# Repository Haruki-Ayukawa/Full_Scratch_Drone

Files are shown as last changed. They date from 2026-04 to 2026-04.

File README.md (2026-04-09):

# Full_Scratch_Drone
## 概要
キットを購入するのではなく<br>
- KiCADで設計し表面実装したESP32搭載制御基板
- 3DCADで設計し3Dプリンタで造形したフレーム
- AmazonやRCヘリドローン専門ショップで購入したモータ・プロペラ・LiPoバッテリ

を用いてフルスクラッチのドローンを製作しました。

## 制御基板
- 構成 → MCU(マイコン)＋IMU(9軸慣性センサ)＋ESC(MOSFET×4個)＋コネクタなどを1枚の基板に搭載しました。
- 部品 → ESP32-MINI-1-N4(MCU)、ICM-20948(IMU)、AO3400A(Nch MOSFET)などなど。
- 購入 → 秋月電子通商　様やcorestaff　様で購入しました。一部のパーツはAmazonで購入しました。
- 基板 → SnapMagicなどでパーツのデータを収集し、KiCADで回路図及びPCB基板を設計後、JLCPCBに発注しました。
- 実装 → ホットプレートやペーストはんだを用いて表面実装しました。

詳細は[control-boardフォルダ](control-board)をご覧ください。

## フレーム
- 設計 → Fusionで設計しました。
- 製造 → 3Dプリンタ(RAISE3D E2　ノズル径0.4mm　フィラメントPLA黒色)で造形しました。

詳細は[frameフォルダ](frame)をご覧ください。

## モータ
- 部品 → [直径8.5mm　長さ20mm　3~5V](https://amzn.asia/d/07lUeh3T)
- 購入 → Amazonで購入しました。

## プロペラ
- 部品 → [マイクロクワッド用55mm Blade Propeller Prop 4pcs](https://wda-jp.com/shop/products/detail/863)
- 購入 → 若狭小浜ドローン協会(WDA) 様の公式オンラインショップで購入しました。

## LiPoバッテリ
- 部品 → [GNB POWER LIPO 550mAh 1s 3.8V 100C コネクタ種：A30](https://helimonster.jp/?pid=176671622)
- 購入 → ヘリモンスター　様で購入しました。

## 制御コード(フライトコントローラ：ドローン側)
- VSCodeでコーディングし、VSCodeの拡張機能であるPlatformIOでコンパイルとビルドを行いました。

詳細は[firmwareフォルダ]()をご覧ください。

## 制御コード(プロポーショナルコントロール送信機：スマホアプリ側)
- MIT App Inventorというブラウザタイプのアプリ開発ツールを用いてスマホをドローンのプロポにしました。

詳細は別のリポジトリ[Example_MITAppInventor_for_DroneController](https://github.com/Haruki-Ayukawa/Example_MITAppInventor_for_DroneController/tree/main)をご覧ください。

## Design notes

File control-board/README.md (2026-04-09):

# control-boardフォルダの中身について
## KiCadフォルダ

## manufacturingフォルダ

## docsフォルダ

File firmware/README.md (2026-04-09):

# firmwareフォルダの中身について
## drone_PID_1フォルダ
VSCode内の拡張機能「PlatformIO」を利用してコーディング・ビルド・コンパイルを行いました。<br>
1_includeフォルダ, 2_libフォルダ, 3_platformio.iniファイル, 4_srcフォルダが入っています。<br>
以下その説明

## 1_includeフォルダ
特に使っていません。

## 2_libフォルダ
特に使っていません。

## 3_platformio.iniファイル
書き込み先のボード種やシリアル通信のbps、インクルードするライブラリを指定するファイルです。

## 4_srcフォルダ
コードの中身になります。<br>
.cppファイルは実際の関数の中身が書かれています。<br>
.hファイルは関数・定数の宣言や必要な外部ライブラリのインクルードが書かれています。<br>
以下簡単な説明

#### control.cppファイルと.h ファイル
- モータをPWMで駆動させる上でのセットアップ関数と実際に駆動させる関数
- ①madgwick.cppで得たロールピッチヨー(RPY)の姿勢角　②interfaceBLE.cppで受け取った角度あるいは角速度の目標値　を元にPID制御する関数

などが書かれています。<br>
単ループ角度PID制御とカスケード制御の両方の関数があります。

#### debug.cppファイルと.h ファイル
- PCとつないだシリアルモニタでデバッグするための関数

が書かれています。

#### imu.cppファイルと.h ファイル
- 9軸IMUセンサのセットアップ関数
- センサのジャイロ値を校正する関数
- センサの9種の値を読み取る関数
- センサにローパスフィルタを掛ける関数

などが書かれています。<br>
なおDLPFの設定を有効にしたため、代わりに4つ目のローパスフィルタを掛ける関数では実際にはフィルタを掛けていません。

#### interfaceBLE.cppファイルと.h ファイル
- BLE通信する上でのセットアップ関数
- 指令がバイナリ通信で来た際に読み取る関数
- こちらからスマホ側へNOTIFY(送信)するための無線デバッグ関数

などが書かれています。<br>
情報工学や通信工学を専攻しておらず初めての経験だったため、**最も難しく、ほとんどchatGPT頼り**になってしまいました。

#### madgwick.cppファイルと.hファイル
- imu.cpp内の読み取り関数で得た9種(6種)の値を元にRPYの姿勢角を計算する関数

が書かれています。<br>
MadgwickfilterAHRS.hライブラリの関数をそのまま使っています。
- ①9軸(ジャイロ3軸＋加速度3軸＋地磁気3軸)
- ②6軸(ジャイロ3軸＋加速度3軸)

①か②か選択できますが、地磁気はモータ回転で発生する電磁場の影響などで上手く行かなかったため現在は②で計算しています。

#### main.cppファイル
- 上記の各種セットアップに関する関数を実行するvoid setup()関数
- BLE通信で指令値更新 → センサの読み取り → MWFで姿勢角取得 → PID計算してモータ出力 → 各種デバッグ送信　を回すvoid loop()関数

が書かれています。<br>
細かい動作仕様は[Example_MITAppInventor_for_DroneController](https://github.com/Haruki-Ayukawa/Example_MITAppInventor_for_DroneController/tree/main)
内のREADMEから飛べるYouTube動画も併せてご覧ください。

#### struct.hファイル
今回のドローンコードでは値の受け渡しに構造体を採用しています。<br>
関連するパラメータを一つのまとまりとして管理でき、コードの可読性および拡張性が向上します。<br>  
特にドローン制御では、位置・速度・姿勢といった多次元データを扱うため、構造体によるデータ管理が適していると考えました。 <br> 
<br>
このファイルでは、各種データ構造の定義を行っています。

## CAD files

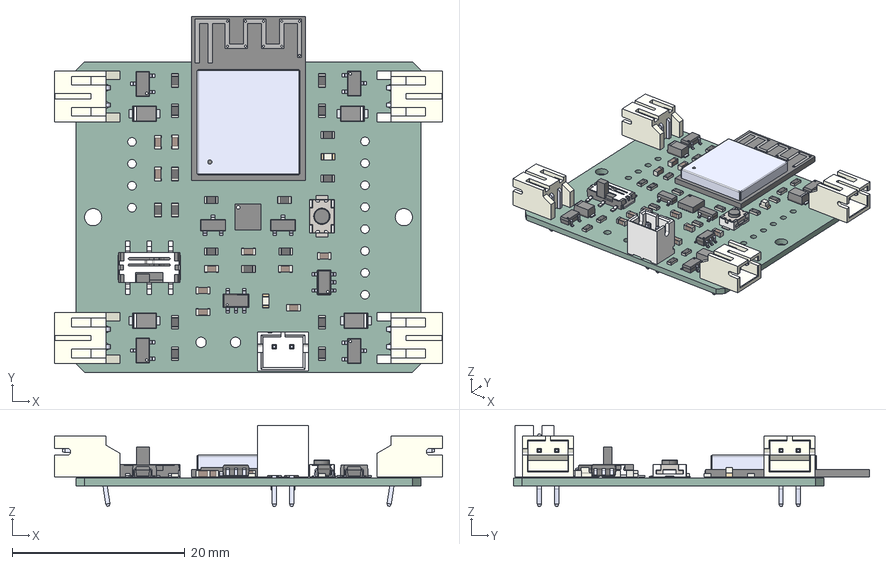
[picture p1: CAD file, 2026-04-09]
control-board/docs/drone_v0-00_pcb.step
45.0 x 41.2 x 9.40 mm
kicad_embedded_EFB9EB6B69339B4832CF7C8FAE120CEA
C_0603_1608Metric x 10
R_0603_1608Metric x 18
PinKIdent x 4
PinK x 4
PinA x 4
kicad_embedded_1087D84B1A9B50382FE17C0D6D803E1A x 4
kicad_embedded_F61AE14A9B6CD33695C6B15B4C50FB9C
LED_0603_1608Metric x 2
kicad_embedded_96822C8A4A191643E8612697CA9D3853
kicad_embedded_640A4FFACB3C051AC2F3E19E366DE6D8
kicad_embedded_2836B2736456D9190677AFF275D22C36
kicad_embedded_1FE01337C3ABB1394D092E43585B70D1 x 4
kicad_embedded_5C4911B6E682F9ABB571BB254287C6B1
kicad_embedded_445924E2E9928FB5B242DCD9D2B32355 x 2
kicad_embedded_AEB765CD93CE368EA6921F6A5A5118E1
drone_v0-01_PCB

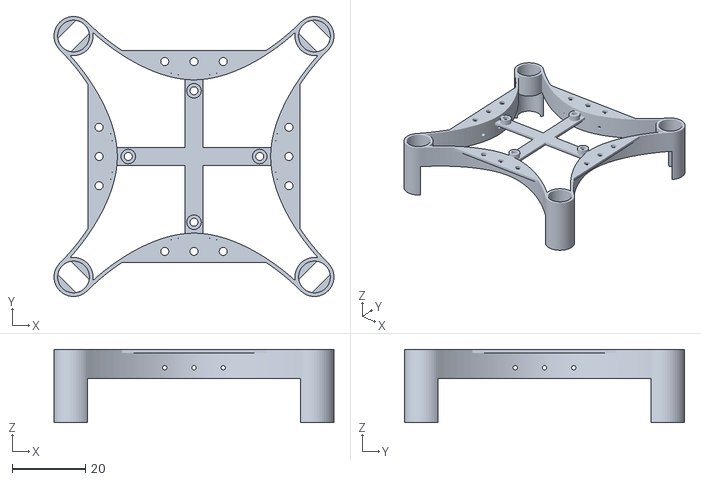
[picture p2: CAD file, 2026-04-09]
frame/drone_v0-03_frame.stl
76.7 x 76.7 x 20.0

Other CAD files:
frame/drone_v0-03_frame.f3d

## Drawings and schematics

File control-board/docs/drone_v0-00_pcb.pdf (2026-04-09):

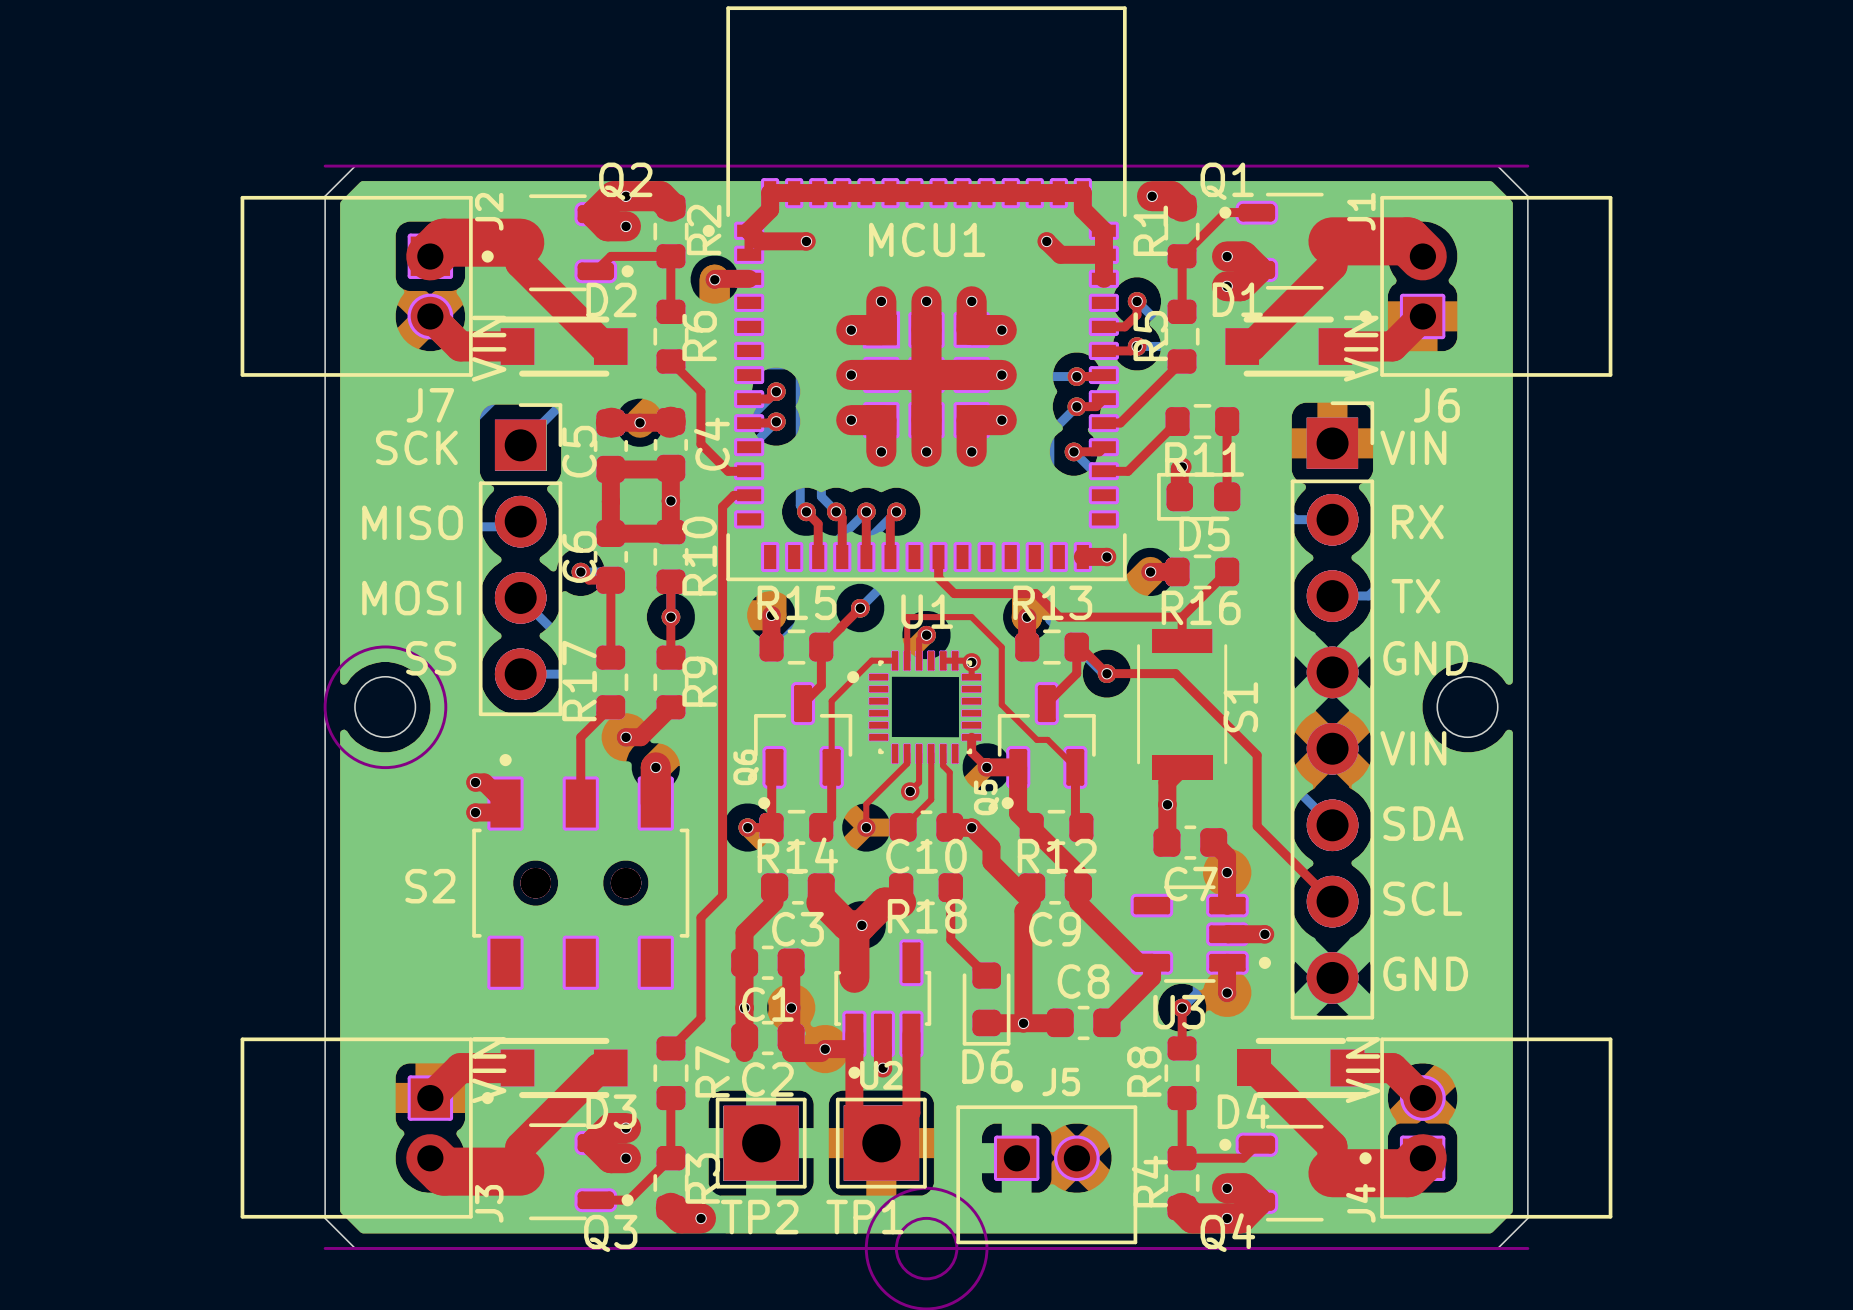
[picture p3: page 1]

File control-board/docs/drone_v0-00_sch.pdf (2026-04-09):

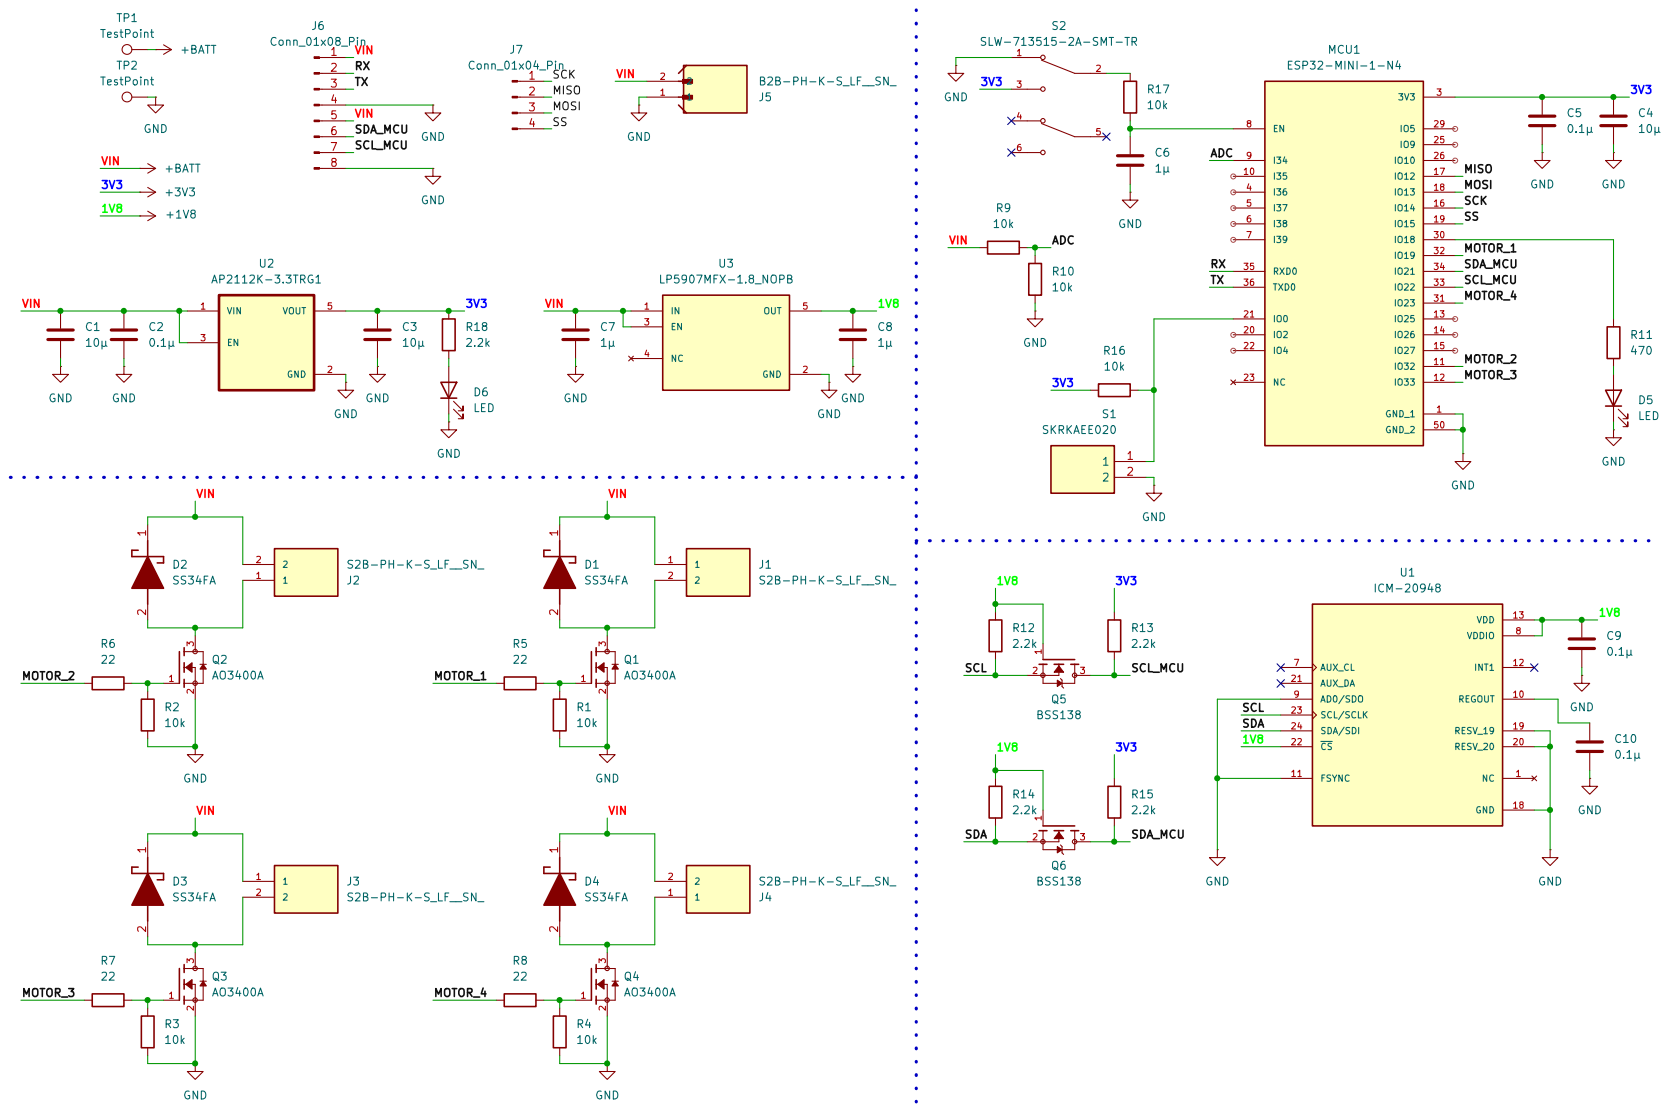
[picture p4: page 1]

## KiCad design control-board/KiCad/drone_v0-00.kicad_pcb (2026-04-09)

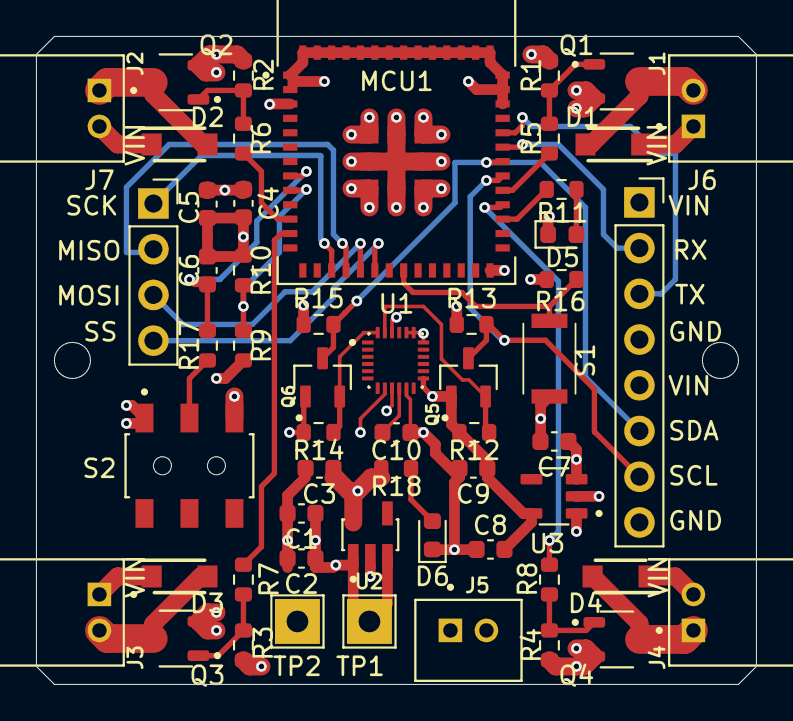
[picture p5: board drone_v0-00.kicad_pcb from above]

Board: 4 copper layers, 40.0 x 36.0 mm, 55 parts (0 on the bottom side), 34 nets.

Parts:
C1, C3, C4: 10µ; C_0603_1608Metric
C2, C5, C9, C10: 0.1µ; C_0603_1608Metric
C6, C7, C8: 1µ; C_0603_1608Metric
D1, D2, D3, D4: SS34FA; SODFL3618X143N
D5, D6: LED; LED_0603_1608Metric
J1, J2, J3, J4: S2B-PH-K-S_LF__SN_; JST_S2B-PH-K-S_LF__SN_
J5: B2B-PH-K-S_LF__SN_; JST_B2B-PH-K-S_LF__SN_
J6: Conn_01x08_Pin; PinSocket_1x08_P2.54mm_Vertical
J7: Conn_01x04_Pin; PinSocket_1x04_P2.54mm_Vertical
MCU1: ESP32-MINI-1-N4; XCVR_ESP32-MINI-1-N4
Q1, Q2, Q3, Q4: AO3400A; SOT95P280X125-3N
Q5, Q6: BSS138; SOT95P240X111-3N
R1, R2, R3, R4, R9, R10, R16, R17: 10k; R_0603_1608Metric
R5, R6, R7, R8: 22; R_0603_1608Metric
R11: 470; R_0603_1608Metric
R12, R13, R14, R15, R18: 2.2k; R_0603_1608Metric
S1: SKRKAEE020
S2: SLW-713515-2A-SMT-TR; SW_SLW-713515-2A-SMT-TR
TP1, TP2: TestPoint; TestPoint_THTPad_2.5x2.5mm_Drill1.2mm
U1: ICM-20948; QFN40P300X300X105-24N
U2: AP2112K-3.3TRG1; SOT95P285X140-5N
U3: LP5907MFX-1.8_NOPB; SOT95P280X145-5N

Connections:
+1V8: C8.1, C9.1, Q5.1, Q6.1, R12.1, R14.1, U1.8 (VDDIO), U1.13 (VDD), U1.22 (~CS), U3.5 (OUT)
+3V3: C3.1, C4.1, C5.1, MCU1.3 (3V3), R13.1, R15.1, R16.1, R18.1, S2.3, U2.5 (VOUT)
+BATT: C1.1, C2.1, C7.1, D1.1 (K), D2.1 (K), D3.1 (K), D4.1 (K), J1.1, J2.2, J3.1, J4.2, J5.2, J6.1, J6.5, R9.1, TP1.1, U2.1 (VIN), U2.3 (EN), U3.1 (IN), U3.3 (EN)
/ADC: MCU1.9 (I34), R9.2, R10.1
/MISO: J7.2, MCU1.17 (IO12)
/MOSI: J7.3, MCU1.18 (IO13)
/MOTOR_1: MCU1.32 (IO19), R5.1
/MOTOR_2: MCU1.11 (IO32), R6.1
/MOTOR_3: MCU1.12 (IO33), R7.1
/MOTOR_4: MCU1.31 (IO23), R8.1
/RX: J6.2, MCU1.35 (RXD0)
/SCK: J7.1, MCU1.16 (IO14)
/SCL: Q5.2, R12.2, U1.23 (SCL/SCLK)
/SCL_MCU: J6.7, MCU1.33 (IO22), Q5.3, R13.2
/SDA: Q6.2, R14.2, U1.24 (SDA/SDI)
/SDA_MCU: J6.6, MCU1.34 (IO21), Q6.3, R15.2
/SS: J7.4, MCU1.19 (IO15)
/TX: J6.3, MCU1.36 (TXD0)
GND: C1.2, C2.2, C3.2, C4.2, C5.2, C6.2, C7.2, C8.2, C9.2, C10.2, D5.1 (K), D6.1 (K), J5.1, J6.4, J6.8, MCU1.1 (GND_1), MCU1.2 (GND_1), MCU1.27 (GND_1), MCU1.38 (GND_1), MCU1.39 (GND_1), MCU1.40 (GND_1), MCU1.41 (GND_1), MCU1.42 (GND_1), MCU1.43 (GND_1), MCU1.44 (GND_1), MCU1.45 (GND_1), MCU1.46 (GND_1), MCU1.47 (GND_1), MCU1.48 (GND_1), MCU1.49 (GND_1), MCU1.50 (GND_2), MCU1.51 (GND_2), MCU1.52 (GND_2), MCU1.53 (GND_2), MCU1.54 (GND_2), MCU1.55_1 (GND_2), MCU1.55_2 (GND_2), MCU1.55_3 (GND_2), MCU1.55_4 (GND_2), MCU1.55_5 (GND_2), MCU1.55_6 (GND_2), MCU1.55_7 (GND_2), MCU1.55_8 (GND_2), MCU1.55_9 (GND_2), Q1.2, Q2.2, Q3.2, Q4.2, R1.2, R2.2, R3.2, R4.2, R10.2, S1.2, S2.1, TP2.1, U1.9 (AD0/SDO), U1.11 (FSYNC), U1.18 (GND), U1.19 (RESV_19), U1.20 (RESV_20), U2.2 (GND), U3.2 (GND)
unnamed: D1.2 (A), J1.2, Q1.3
unnamed: D2.2 (A), J2.1, Q2.3
unnamed: D3.2 (A), J3.2, Q3.3
unnamed: D4.2 (A), J4.1, Q4.3
unnamed: D5.2 (A), R11.2
unnamed: D6.2 (A), R18.2
unnamed: C6.1, MCU1.8 (EN), R17.2
unnamed: MCU1.21 (IO0), R16.2, S1.1
unnamed: MCU1.30 (IO18), R11.1
unnamed: Q1.1, R1.1, R5.2
unnamed: Q2.1, R2.1, R6.2
unnamed: Q3.1, R3.1, R7.2
unnamed: Q4.1, R4.1, R8.2
unnamed: R17.1, S2.2
unnamed: C10.1, U1.10 (REGOUT)
